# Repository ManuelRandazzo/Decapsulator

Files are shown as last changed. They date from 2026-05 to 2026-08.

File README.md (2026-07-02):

# Decapsulator
<p align="center">
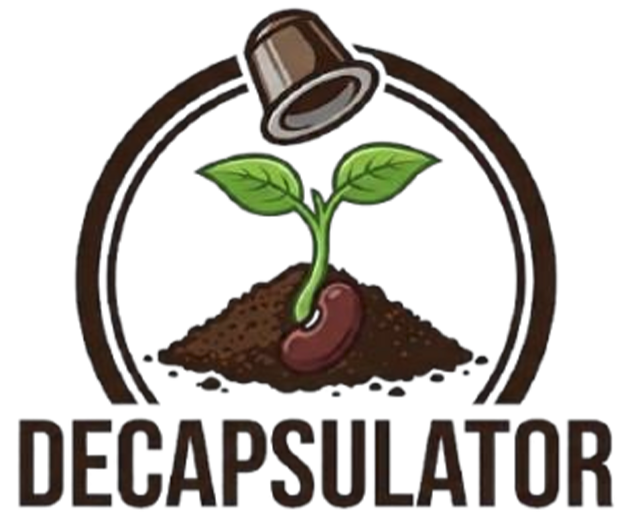
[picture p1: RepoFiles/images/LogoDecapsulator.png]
  
</p>

<p align="center">
  <em>Repo condiviso con il Gruppo 1 ITS 24-26 con programma del macchinario</em>
</p>

---

## Overview
**Decapsulator** è il prototipo di un macchinario nato con lo scopo principale di ridurre rifiuti secchi automatizzando un processo ripetitivo, che tende ad essere evitato e talvolta può diventare pericoloso se non si prestano le dovute attenzioni che è quello di aprire le capsule esauste per poter separare il caffè dall'involucro esterno.

**Sedi**: 
- **IIS Einaudi-Scarpa** : Via Sansovino, 6, 31044 Montebelluna (TV)
- **IPSIA Barsanti-Galilei** : Via Avenale, 6, 31033 Castelfranco Veneto (TV) 

---

## Intended Use 
Prototipo a scopo didattico, non destinato alla vendita o all'uso continuativo. In caso di vendita a scopo commerciale saranno da integrare tutti i dispositivi di sicurezza descritti nelle norme vigenti nella data di revisione e modifica del prototipo successiva a quella descritta dal documento di uso e manutenzione. 

---

## Features
- Automatizzazione della separazione delle capsule dal caffè
- Orientato alla facilità di utilizzo e di manutenzione
- FreeRTOS per avere un controllo real time del processo
- Sicurezza del macchinario
- Prototipo modulabile per diversi tipi di capsule cambiando pochissimi componenti
- Il suo sviluppo ha contribuito in piccola parte al mondo dell'Open Hardware di disegni CAD 3D.
- Design compatto rivolto ad un ambiente domestico

---

## Authors
- ***Manuel Randazzo*** - Firmware Designer, Backend Firmware Developer, Integration Developer, Firmware Tester, Electrical Designer, Electrical tester, Mechanical Designer, Documentation Contributor.
- ***Alessio Pisan*** - Electrical Designer, Electrical Tester, Frontend Firmware Developer, Backend Firmware Developer, Firmware Tester, Documentation Contributor.
- ***Riccardo Pavanetto*** - Mechanical Designer, Mechanical Designer
- ***Federico Dorigo*** - Scrum Master, Procurement Coordinator, Documentation Coordinator, Payroll Administrator
- ***Christian Poletti*** - Documentation Contributor
- ***Arun James Thanamcheril*** - Documentation Contributor

<p align="center">
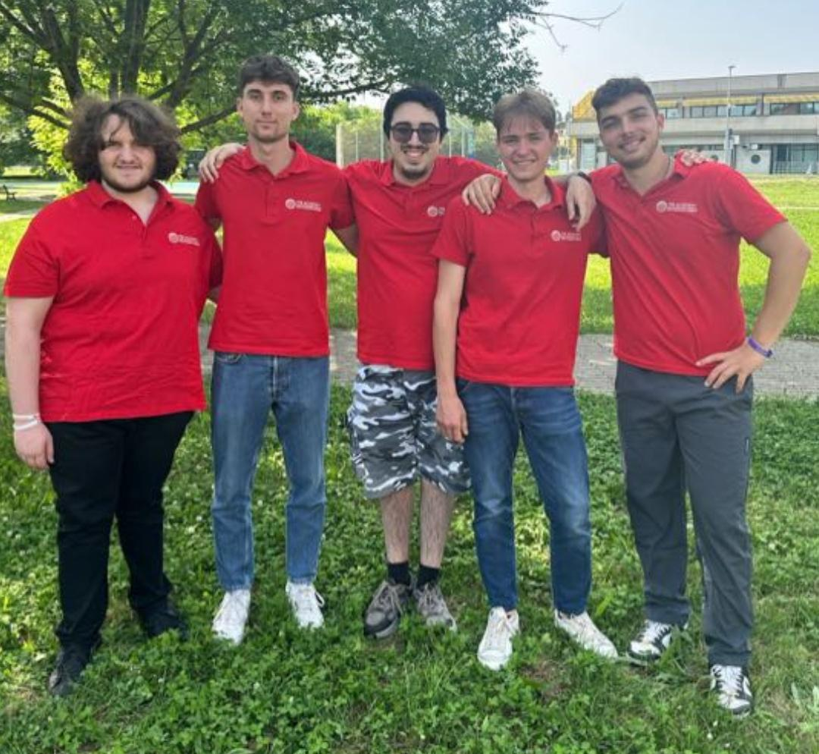
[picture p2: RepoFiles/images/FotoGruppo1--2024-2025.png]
  
</p>
<p align="center">
    <em>Foto del gruppo 1 ITS 24-25 - foto scattata nel 2025.</em>
    <em>Partendo da sinistra : Manuel, Christian, Alessio, Riccardo e Federico</em>
</p>

<p align="center">
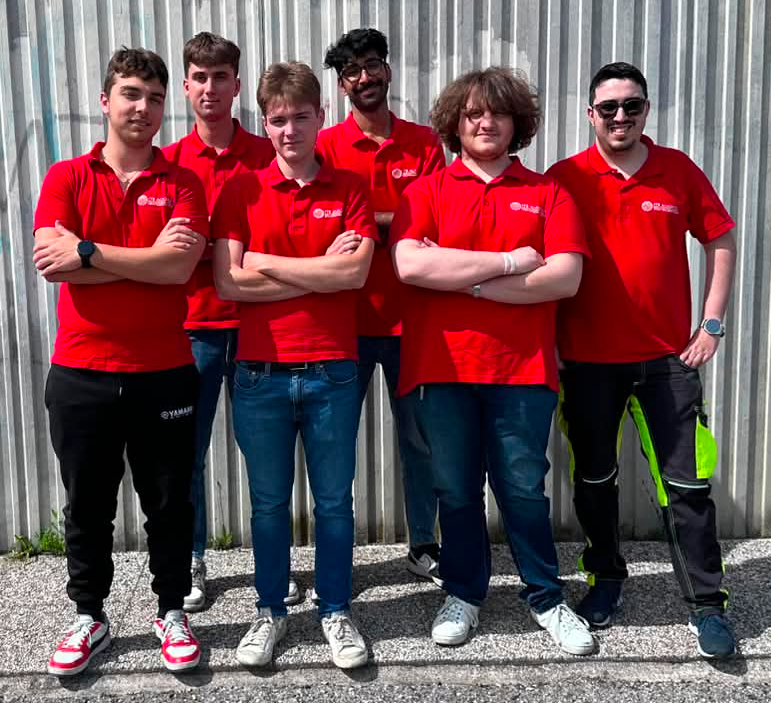
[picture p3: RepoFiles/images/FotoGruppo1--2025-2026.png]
  
</p>
<p align="center">
    <em>Foto del gruppo 1 ITS 25-26 - foto scattata nel 2026.</em>
    <em>Partendo da sinistra : Federico, Christian, Riccardo, Arun James, Manuel e Alessio</em>
</p>

---

## Dichiarazione Di Conformità CE Del Prototipo
Il presente prototipo è stato progettato seguendo i criteri di sicurezza delle varie direttive:  
- ***Direttiva Macchine 2006/42/CE***: Poiché l'apparecchio presenta organi in movimento, tra cui tamburo rotante, paratia di selezionatura servo-attivata e punzone, i quali comportano rischi meccanici.

- ***Direttiva Bassa Tensione (LVD) 2014/35/UE***: Consultata per la sicurezza dei componenti elettrici e dei circuiti di alimentazione.

- ***Direttiva Compatibilità Elettromagnetica (EMC) 2014/30/UE***: Applicabile per garantire che l’elettronica non interferisca con altre apparecchiature circostanti al macchinario.

- ***Direttiva RoHS 2011/65/UE***: Consultata per garantire l'assenza di sostanze pericolose nei componenti elettronici e nei materiali di apporto. 

Norme armonizzate applicate :
- ***UNI EN ISO 12100:2010***: Sicurezza del macchinario - Principi generali di progettazione - Valutazione e attenuazione del rischio. 

- ***UNI EN ISO 13857:2020***: Distanze di sicurezza per impedire il raggiungimento di zone pericolose con gli arti superiori (utilizzata per dimensionare l'imbocco delle capsule e i carter del tamburo).

- ***UNI EN ISO 14119:2013***: Dispositivi di interblocco associati ai ripari (utilizzata per la scelta e l'installazione del micro-switch di sicurezza sul coperchio).

- ***CEI EN 60204-1***: Sicurezza dell'equipaggiamento elettrico delle macchine (utilizzata per lo schema elettrico e funzionale). 

---

## Disegno Prototipo E Componenti Principali
- ### **Parte Meccanica**
<p align="center">
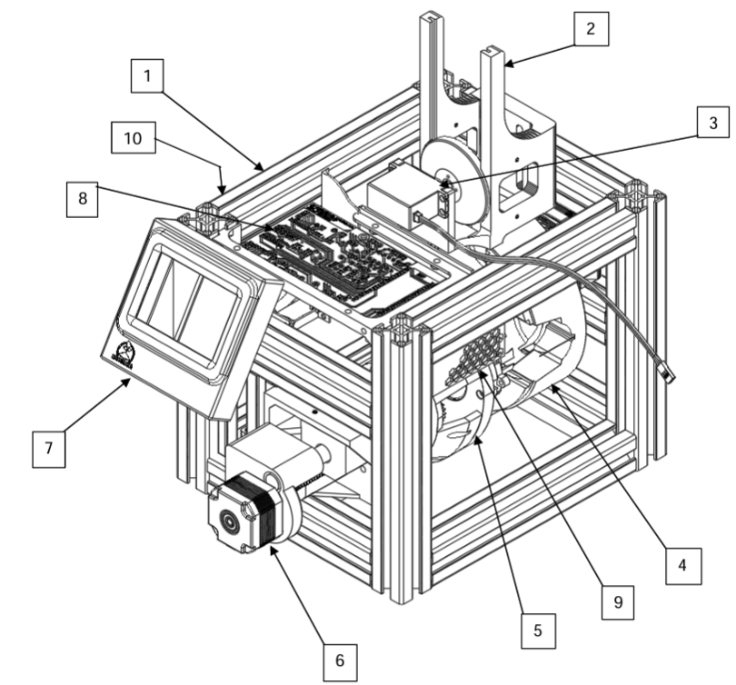
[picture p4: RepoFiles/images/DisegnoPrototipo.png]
  
</p>

<p align="center">
  <em>Figura 1 — Architettura generale del Decapsulator</em>
</p>
 
**Tabella Componenti :**

| N° |  Descrizione  |
|----|---|
| 1  | Profili in alluminio 30x30 cm |
| 2  | Magazzino verticale capsule |
| 3  | Paratia di selezionatura servoattivata del magazzino verticale |
| 4  | Tamburo di posizionamento |
| 5  | Zona di Punzonatura e Raschiatura |
| 6  | Motore passo-passo del Punzone e Raschiatore |
| 7  | Display dell’interfaccia uomo-macchina (HMI) |
| 8  | Scheda elettronica |
| 9  | Griglia di protezione parte elettronica |
| 10 | Ventola di raffreddamento (lato sinistro del macchinario) |

<p align="center">
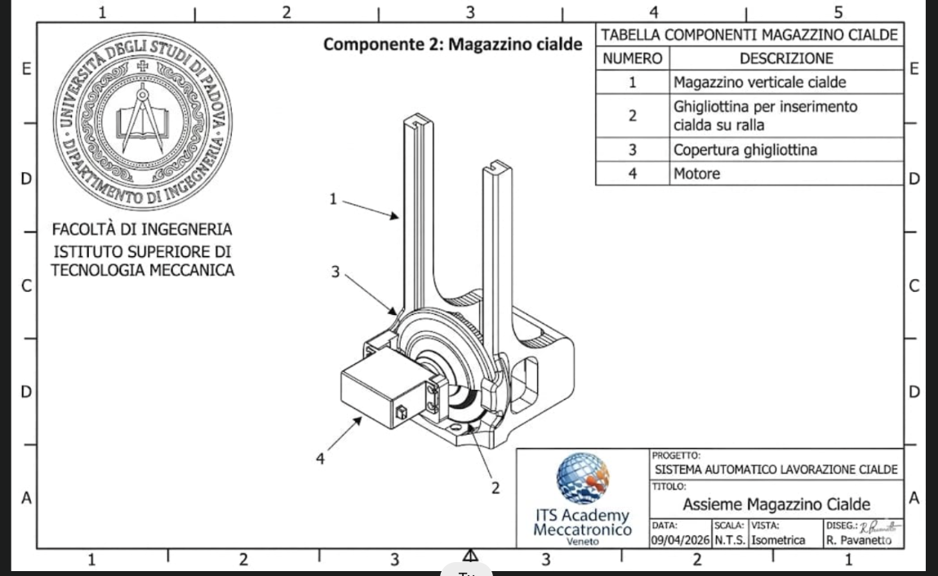
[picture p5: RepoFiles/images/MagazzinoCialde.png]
  
</p>

<p align="center">
  <em>Figura 2 — Magazzino Cialde : Serve per stoccare le capsule prima che vengano </em>
</p>

<p align="center">
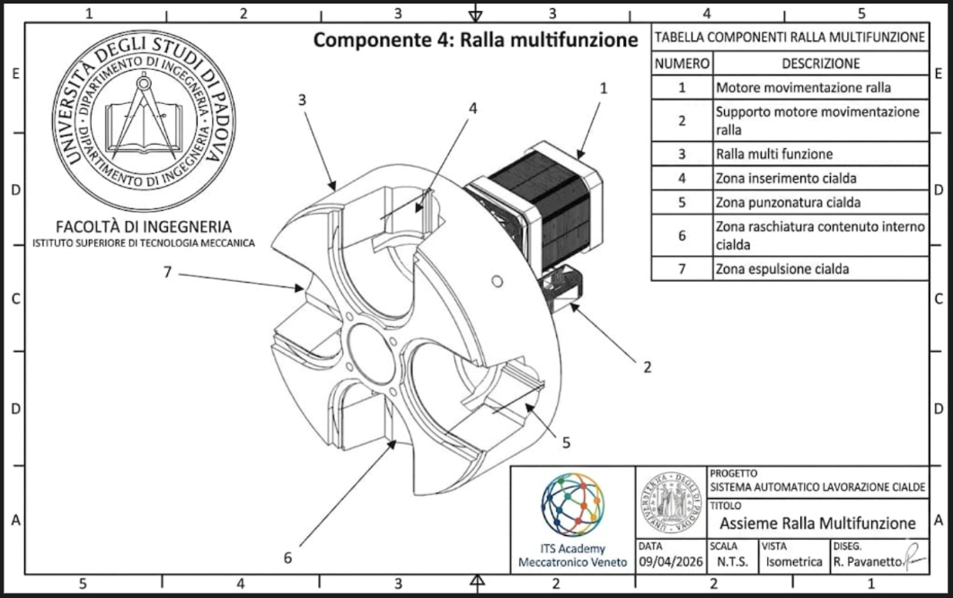
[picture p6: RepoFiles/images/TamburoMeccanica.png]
  
</p>

<p align="center">
  <em>Figura 3 — Tamburo : Serve per trasportare la capsula nelle varie fasi di lavorazione (Acquisizione, Punzonatura, Raschiatura, Espulsione)</em>
</p>

- ### **Parte Elettronica**

<p align="center">
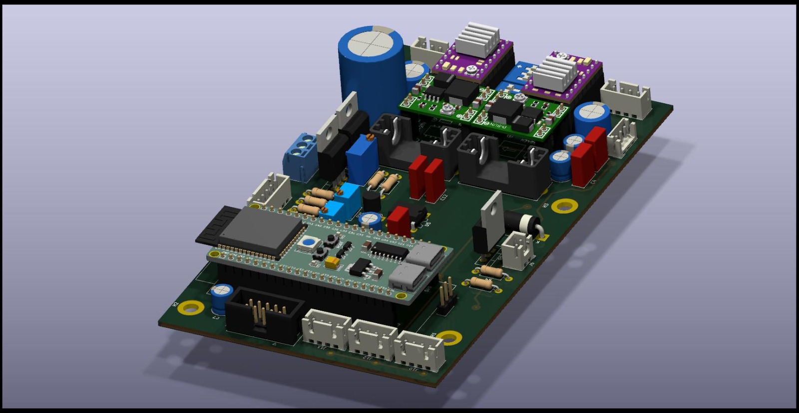
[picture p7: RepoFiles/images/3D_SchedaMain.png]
  
</p>

<p align="center">
  <em>Figura 4 — Scheda di controllo del Decapsulator</em>
</p>

<p align="center">
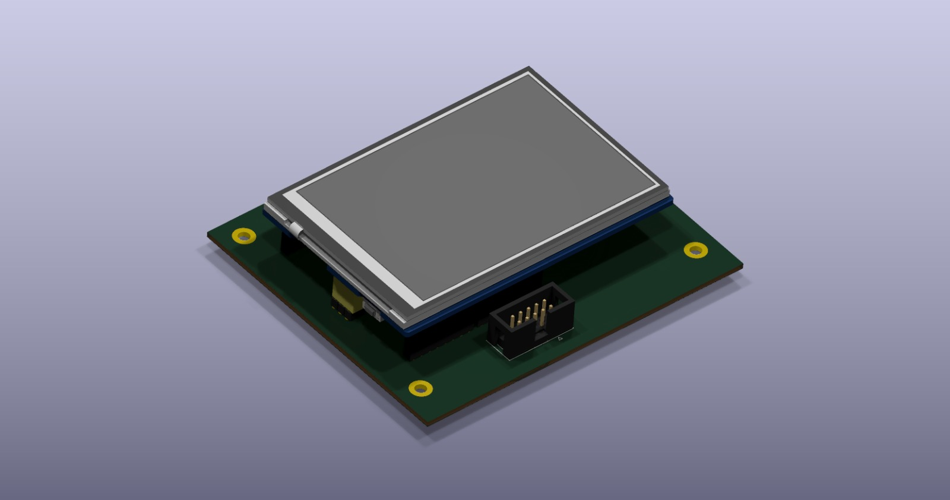
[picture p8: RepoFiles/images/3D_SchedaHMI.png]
  
</p>

<p align="center">
  <em>Figura 5 — Scheda HMI del Decapsulator</em>
</p>

<p align="center">
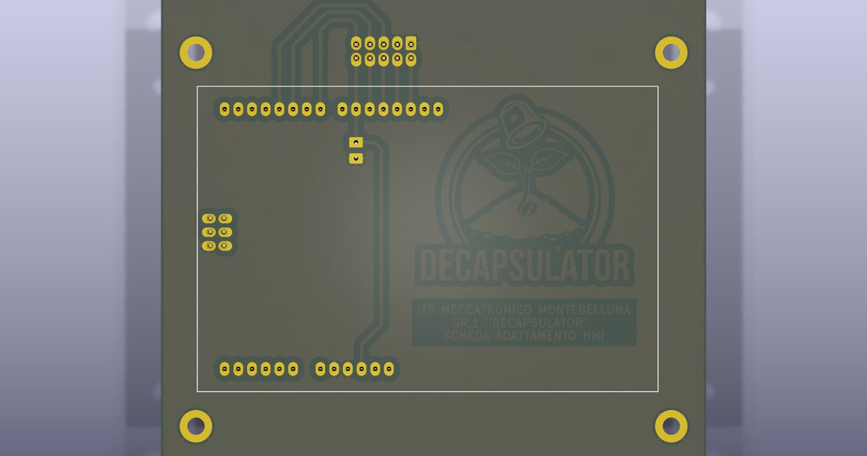
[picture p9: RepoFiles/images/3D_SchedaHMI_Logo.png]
  
</p>

<p align="center">
  <em>Figura 5 — Scheda HMI del Decapsulator - Vista retro</em>
</p>

<p align="center">
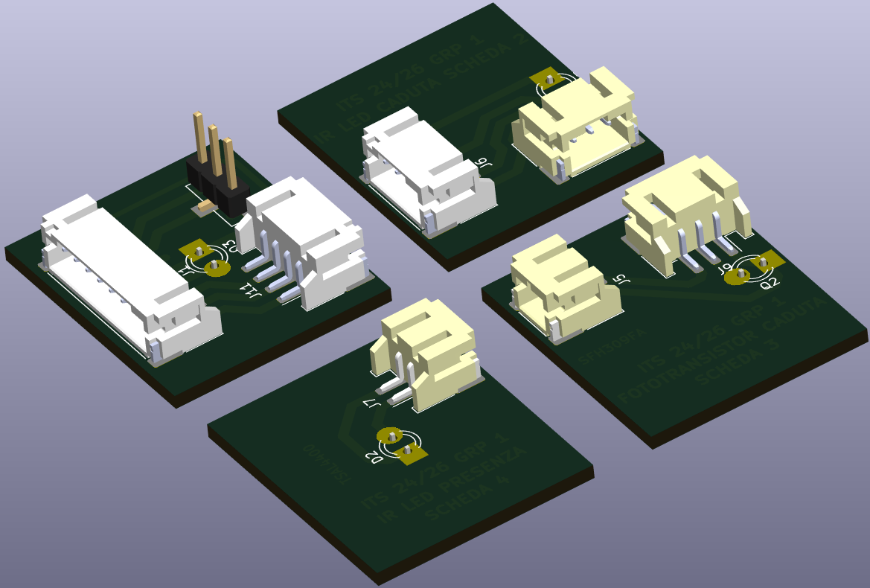
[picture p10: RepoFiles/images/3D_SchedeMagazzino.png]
  
</p>

<p align="center">
  <em>Figura 6 — Schede del "Magazzino Cialde" del Decapsulator, rappresentano due foto transistor e due LED IR, inoltre su una scheda è presente il connettore 3 poli del servomotore della "Paratia"</em>
</p>

---

## Sequenza Di Funzionamento Automatico Del Decapsulator
Il "Decapsulator" quando viene pilotato in modalità automatica per aprire le capsule di caffè segue questo diagramma :
<p align="center">
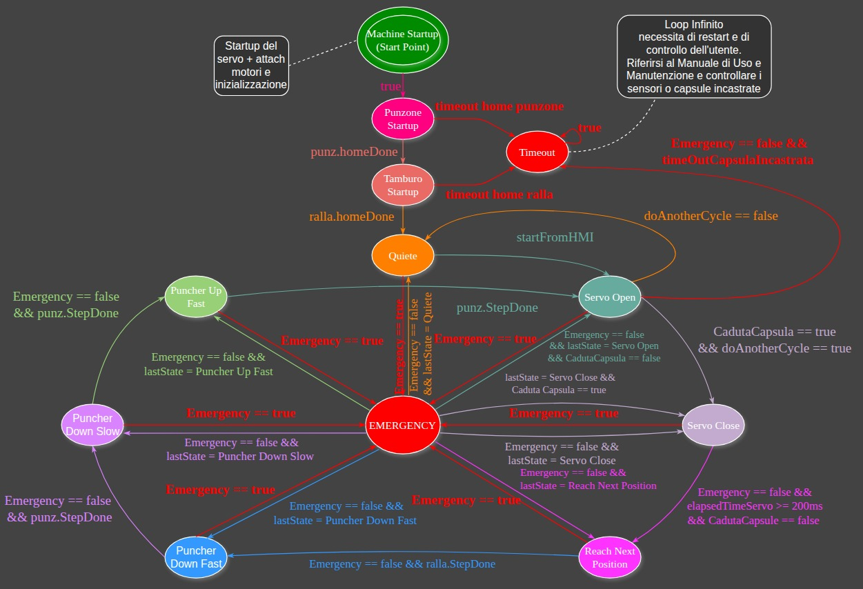
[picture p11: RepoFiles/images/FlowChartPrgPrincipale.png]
  
</p>

Il quale temporalmente si traduce in questa sequenza osservando i componenti :
<p align="center">
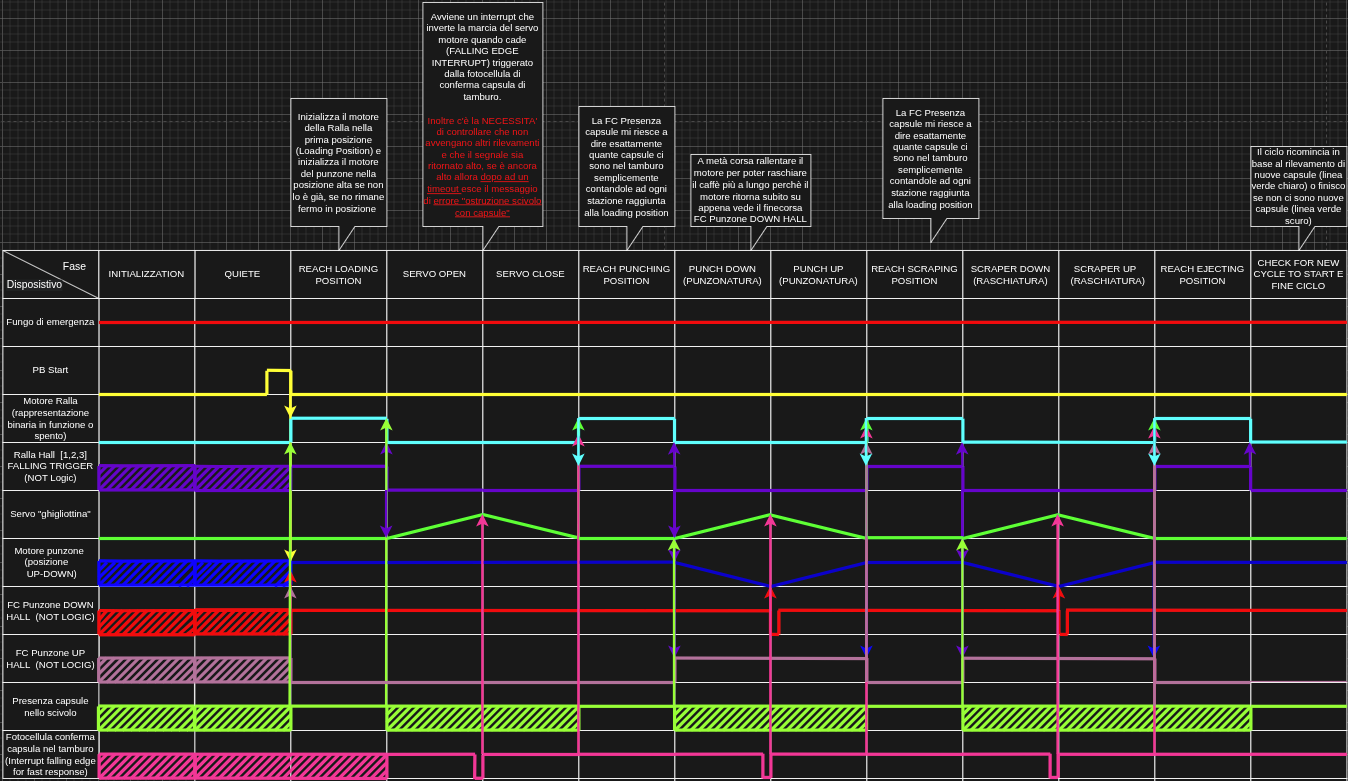
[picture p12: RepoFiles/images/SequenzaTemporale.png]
  
</p>

---

## Dati Sui Motori Utilizzati
Le librerie del driver DRV8825 sono state sviluppate interamente da Manuel Randazzo il quale si è preoccupato di studiare e testare l'hardware, consultare la documentazione ufficiale per poter integrare al meglio la libreria che può essere inclusa così :
```C++
#include "DRV8825_Decapsulator.hpp"
```
oppure includendo la libreria del Motion Controller che già utilizza internamente la precedente libreria e che permette una gestione più semplice del Motore :
```C++
#include "MotionControl.hpp"
```

**Flow chart MotionController**
<p align="center">
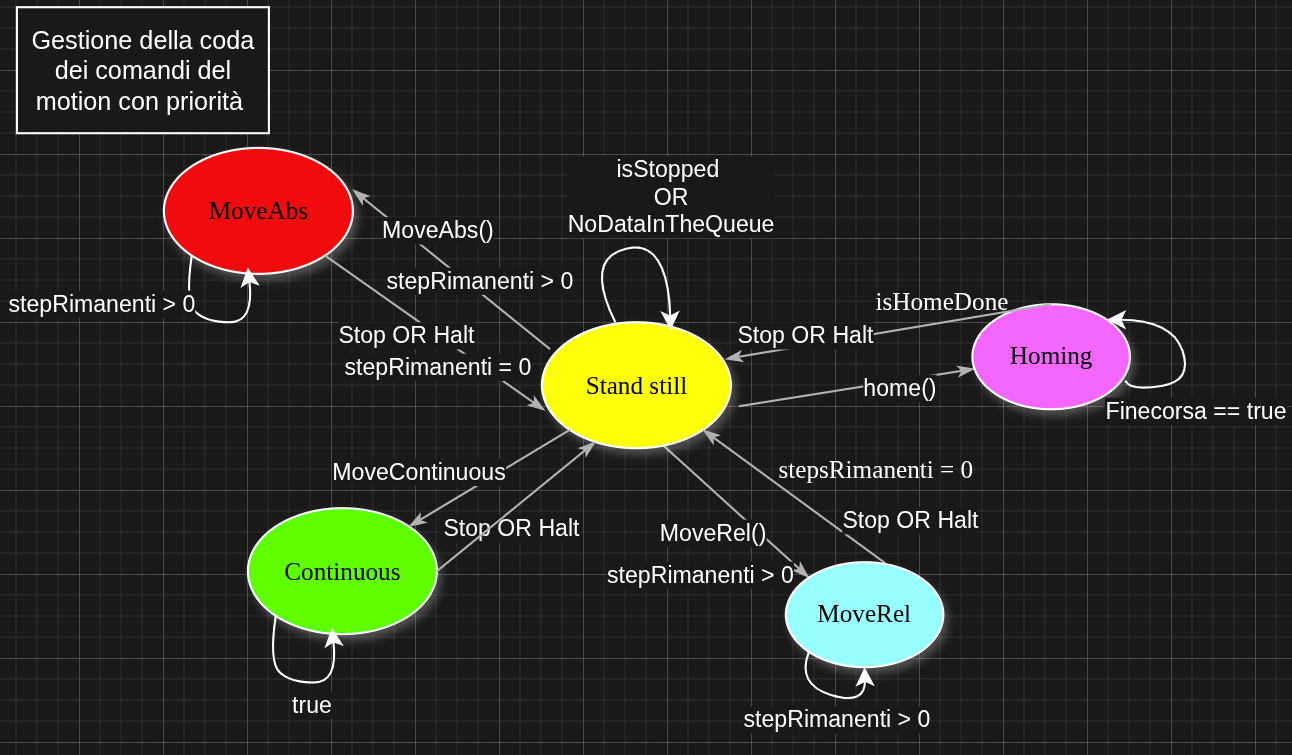
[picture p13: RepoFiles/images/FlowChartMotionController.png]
  
</p>

<p align="center">
  <em>Figura 7 — Flow chart MotionController</em>
</p>

**Simulazione Grafico Coppia-Velocità Motori Stepper**
<p align="center">
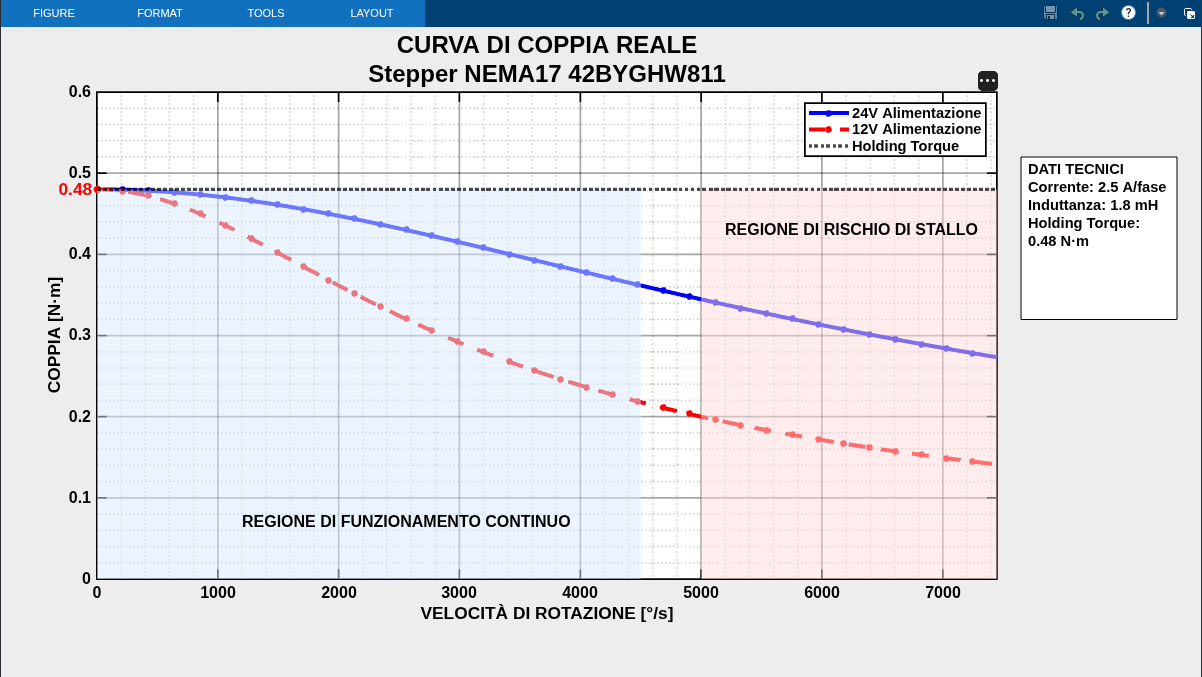
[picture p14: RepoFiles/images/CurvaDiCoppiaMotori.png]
  
</p>

<p align="center">
  <em>Figura 8 — Simulazione curva di coppia dei motori stepper con MATLAB</em>
</p>

---

## Diagnostica E Troubleshooting
Vi è una sezione dedicata per accedere alle impostazioni del manutentore direttamente dall'HMI del macchinario.

Per aiutare il manutentore ad individuare i problemi è possibile ottenere dei privilegi elevati attraverso un login e di conseguenza accedere alla pagina di diagnostica composta dal registro eventi (***Log***) del macchinario e dal movimento manuale (***Jog***) dei motori passo-passo del tamburo rotante e del punzone.

Per maggiori informazioni riguardo a come utilizzare la pagina di manutenzione consultare il manuale di uso e manutenzione alla sezione ***"9.4 Manutenzione tramite pagina di diagnostica sull’interfaccia utente"***.

- Come accedere alla pagina di diagnostica dalla GUI:  

1. Individuare nella pagina principale l’icona dell’ingranaggio indicata in figura
<p align="center">
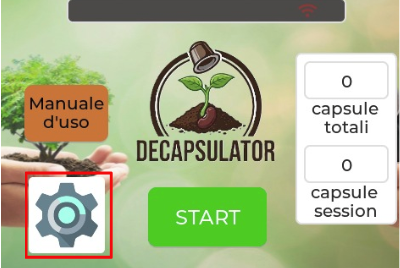
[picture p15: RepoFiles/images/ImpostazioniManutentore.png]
  
</p>

2. Inserire la password unica fornita ai manutentori specializzati
<p align="center">
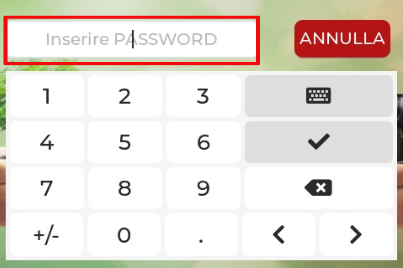
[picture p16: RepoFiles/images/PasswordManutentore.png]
  
</p>

- Come navigare nella pagina di diagnostica dalla GUI, riferimento alla sezione 9.4 del manuale di uso e manutenzione:  

1. Se si vogliono visualizzare i ***LOG*** del macchinario premere il pulsante "Logger" in alto a sinistra della pagina di diagnostica come in figura:
<p align="center">
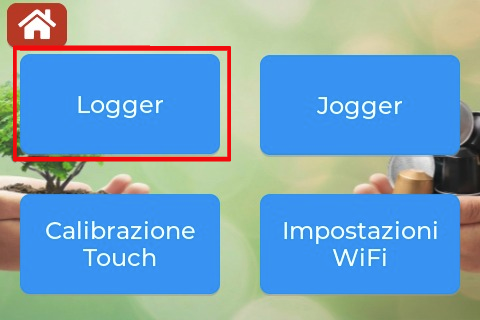
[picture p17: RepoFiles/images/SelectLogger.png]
  
</p>

1.1. Una volta selezionato il Logger si vedrà questa pagina da cui si potrà refreshare i logs oppure cancellarli per avere una pagina più pulita con i tasti in figura:
<p align="center">
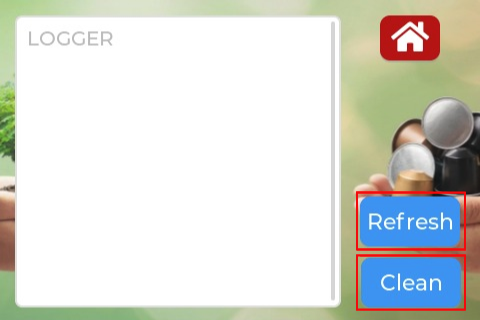
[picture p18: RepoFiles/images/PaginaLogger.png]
  
</p>

2. Se si vogliono comandare in modalità manuale i motori del macchinario con il ***JOG*** premere il pulsante "Jogger" in alto a destra della pagina di diagnostica come in figura:
<p align="center">
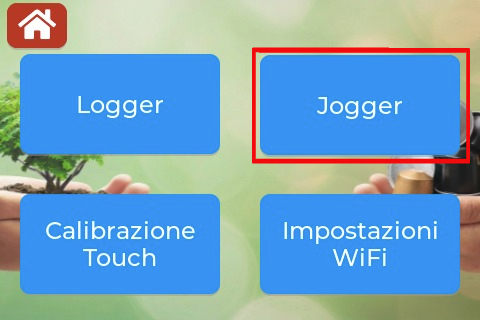
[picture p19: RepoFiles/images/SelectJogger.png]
  
</p>

2.1. Nota: non sarà possibile aggedere alla pagina "Jogger" se il ciclo automatico è stato avviato e non è stato messo in STOP oppure non è finito e si potrà vedere il seguente messaggio:
<p align="center">
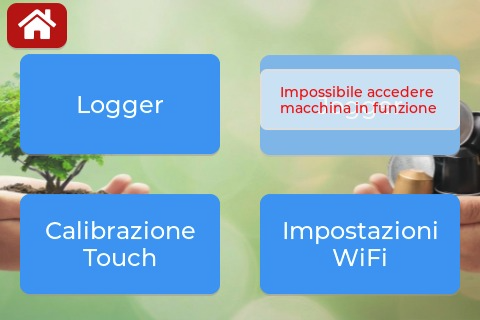
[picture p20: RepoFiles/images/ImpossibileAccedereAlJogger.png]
  
</p>

2.2. Una volta selezionato il Jogger si vedrà questa pagina da cui si potrà comandare indipendemente i motori e visualizzare gli stati dei sensori di finecorsa:
<p align="center">
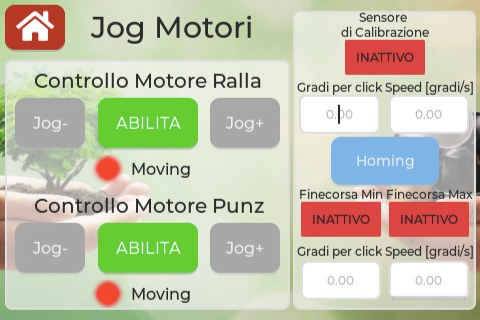
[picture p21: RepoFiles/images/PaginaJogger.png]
  
</p>

3. Se si vuole calibrare il display touch premere il pulsante in basso a sinistra della pagina di diagnostica e seguire le istruzioni fornite a display come in figura:
<p align="center">
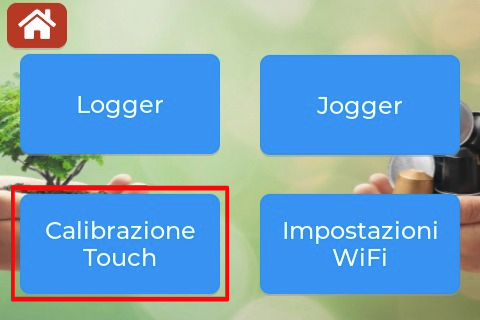
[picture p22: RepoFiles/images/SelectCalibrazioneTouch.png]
  
</p>

4. Se si vogliono inserire nuove credenziali per il WiFi premere il pulsante in basso a destra della pagina di diagnostica come in figura:
<p align="center">
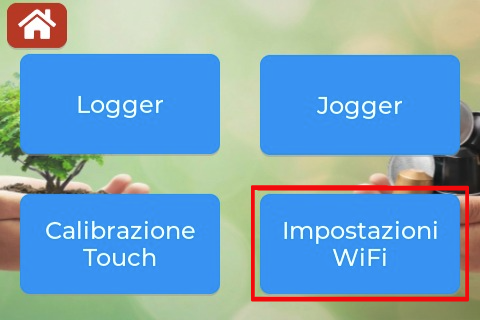
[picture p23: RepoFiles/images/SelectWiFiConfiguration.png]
  
</p>

4.1. Una volta selezionata la pagina di configurazione del WiFi verrà visualizzata questa pagina:
<p align="center">
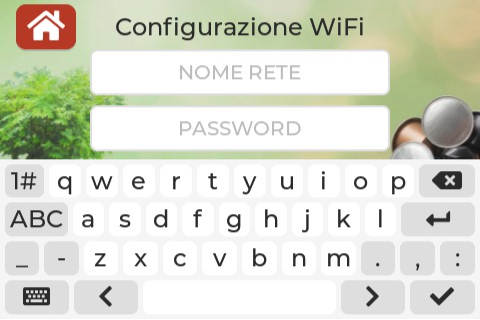
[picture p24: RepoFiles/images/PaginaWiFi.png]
  
</p>

<p align="center">
  <em>Nota : il WiFi consente al macchinario di fare l'upload del firmware tramite Over The Air (OTA), di far loggare in MQTT i messaggi del macchinario e soprattutto di sincronizzare il Real Time Clock (RTC) tramite server NTP così da visualizzare l'ora esatta</em>
</p>

---

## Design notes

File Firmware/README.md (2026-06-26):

# Decapsulator
<p align="center">
  
</p>

<p align="center">
  <em>Repo condiviso con il Gruppo 1 ITS 24-26 con programma del macchinario</em>
</p>

---

## Overview
**Decapsulator** è il prototipo di un macchinario nato con lo scopo principale di ridurre rifiuti secchi automatizzando un processo ripetitivo, che tende ad essere evitato e talvolta può diventare pericoloso se non si prestano le dovute attenzioni che è quello di aprire le capsule esauste per poter separare il caffè dall'involucro esterno.

**Sedi**: 
- Via Sansovino, 6, 31044 Montebelluna (TV)
- Via Avenale, 6, 31033 Castelfranco Veneto (TV) 

---

## Intended use 
Prototipo a scopo didattico, non destinato alla vendita o all'uso continuativo. In caso di vendita a scopo commerciale saranno da integrare tutti i dispositivi di sicurezza descritti nelle norme vigenti nella data di revisione e modifica del prototipo successiva a quella descritta dal documento di uso e manutenzione. 

---

## Features
- Automatizzazione della separazione delle capsule dal caffè
- Orientato alla facilità di utilizzo e di manutenzione
- FreeRTOS per avere un controllo real time del processo
- Sicurezza del macchinario
- Prototipo modulabile per diversi tipi di capsule cambiando pochissimi componenti
- Il suo sviluppo ha contribuito in piccola parte al mondo dell'Open Hardware di disegni CAD 3D.
- Design compatto rivolto ad un ambiente domestico

---

## Authors
- ***Manuel Randazzo*** - Software Designer, Backend Software Developer, Integration Developer, Software Tester, Electrical Designer, Electrical tester, Mechanical Designer.
- ***Alessio Pisan*** - Electrical Designer, Electrical Tester, Frontend Software Developer, Backend Software Developer, Software Tester.
- ***Riccardo Pavanetto*** - Mechanical Designer, Mechanical Designer
- ***Federico Dorigo*** - Scrum Master, Procurement Coordinator, Documentation Coordinator, Payroll Administrator
- ***Christian Poletti*** - Documentation Contributor
- ***Arun James Thanamcheril*** - Documentation Contributor

<p align="center">
  
</p>
<p align="center">
    <em>Foto del gruppo 1 ITS 24-25 - foto scattata nel 2025</em>
    <em>Partendo da sinistra : Manuel, Christian, Alessio, Riccardo e Federico</em>
</p>

<p align="center">
  
</p>
<p align="center">
    <em>Foto del gruppo 1 ITS 25-26 - foto scattata nel 2026</em>
    <em>Partendo da sinistra : Federico, Christian, Riccardo, Arun James, Manuel e Alessio</em>
</p>

---

## Dichiarazione di Conformità CE del prototipo
Il presente prototipo è stato progettato seguendo i criteri di sicurezza delle varie direttive:  
- ***Direttiva Macchine 2006/42/CE***: Poiché l'apparecchio presenta organi in movimento, tra cui tamburo rotante, paratia di selezionatura servo-attivata e punzone, i quali comportano rischi meccanici.

- ***Direttiva Bassa Tensione (LVD) 2014/35/UE***: Consultata per la sicurezza dei componenti elettrici e dei circuiti di alimentazione.

- ***Direttiva Compatibilità Elettromagnetica (EMC) 2014/30/UE***: Applicabile per garantire che l’elettronica non interferisca con altre apparecchiature circostanti al macchinario.

- ***Direttiva RoHS 2011/65/UE***: Consultata per garantire l'assenza di sostanze pericolose nei componenti elettronici e nei materiali di apporto. 

Norme armonizzate applicate :
- ***UNI EN ISO 12100:2010***: Sicurezza del macchinario - Principi generali di progettazione - Valutazione e attenuazione del rischio. 

- ***UNI EN ISO 13857:2020***: Distanze di sicurezza per impedire il raggiungimento di zone pericolose con gli arti superiori (utilizzata per dimensionare l'imbocco delle capsule e i carter del tamburo).

- ***UNI EN ISO 14119:2013***: Dispositivi di interblocco associati ai ripari (utilizzata per la scelta e l'installazione del micro-switch di sicurezza sul coperchio).

- ***CEI EN 60204-1***: Sicurezza dell'equipaggiamento elettrico delle macchine (utilizzata per lo schema elettrico e funzionale). 

---

## Disegno prototipo e Componenti Principali
- ### **Parte Meccanica**
<p align="center">
  
</p>

<p align="center">
  <em>Figura 1 — Architettura generale del Decapsulator</em>
</p>
 
**Tabella Componenti :**

| N° |  Descrizione  |
|----|---|
| 1  | Profili in alluminio 30x30 cm |
| 2  | Magazzino verticale capsule |
| 3  | Paratia di selezionatura servoattivata del magazzino verticale |
| 4  | Tamburo di posizionamento |
| 5  | Zona di Punzonatura e Raschiatura |
| 6  | Motore passo-passo del Punzone e Raschiatore |
| 7  | Display dell’interfaccia uomo-macchina (HMI) |
| 8  | Scheda elettronica |
| 9  | Griglia di protezione parte elettronica |
| 10 | Ventola di raffreddamento (lato sinistro del macchinario) |

<p align="center">
  
</p>

<p align="center">
  <em>Figura 2 — Magazzino Cialde : Serve per stoccare le capsule prima che vengano </em>
</p>

<p align="center">
  
</p>

<p align="center">
  <em>Figura 3 — Tamburo : Serve per trasportare la capsula nelle varie fasi di lavorazione (Acquisizione, Punzonatura, Raschiatura, Espulsione)</em>
</p>

- ### **Parte Elettronica**

<p align="center">
  
</p>

<p align="center">
  <em>Figura 4 — Scheda di controllo del Decapsulator</em>
</p>

<p align="center">
  
</p>

<p align="center">
  <em>Figura 5 — Scheda HMI del Decapsulator</em>
</p>

<p align="center">
  
</p>

<p align="center">
  <em>Figura 5 — Scheda HMI del Decapsulator - Vista retro</em>
</p>

<p align="center">
  
</p>

<p align="center">
  <em>Figura 6 — Schede del "Magazzino Cialde" del Decapsulator, rappresentano due foto transistor e due LED IR, inoltre su una scheda è presente il connettore 3 poli del servomotore della "Paratia"</em>
</p>

---

## Dati Sui Motori Utilizzati
Le librerie del driver DRV8825 sono state sviluppate interamente da Manuel Randazzo il quale si è preoccupato di studiare e testare l'hardware, consultare la documentazione ufficiale per poter integrare al meglio la libreria che può essere inclusa così :
```C++
#include "DRV8825_Decapsulator.hpp"
```
oppure includendo la libreria del Motion Controller che già utilizza internamente la precedente libreria e che permette una gestione più semplice del Motore :
```C++
#include "MotionControl.hpp"
```

**Flow chart MotionController**
<p align="center">
  
</p>

<p align="center">
  <em>Figura 7 — Flow chart MotionController</em>
</p>

**Simulazione Grafico Coppia-Velocità Motori Stepper**
<p align="center">
  
</p>

<p align="center">
  <em>Figura 8 — Simulazione curva di coppia dei motori stepper con MATLAB</em>
</p>

---

## Diagnostica e Troubleshooting
Vi è una sezione dedicata per accedere alle impostazioni del manutentore direttamente dall'HMI del macchinario.

Per aiutare il manutentore ad individuare i problemi è possibile ottenere dei privilegi elevati attraverso un login e di conseguenza accedere alla pagina di diagnostica composta dal registro eventi (***Log***) del macchinario e dal movimento manuale (***Jog***) dei motori passo-passo del tamburo rotante e del punzone. 

Come accedervi:  
1. Individuare nella pagina principale l’icona dell’ingranaggio indicata in figura
<p align="center">
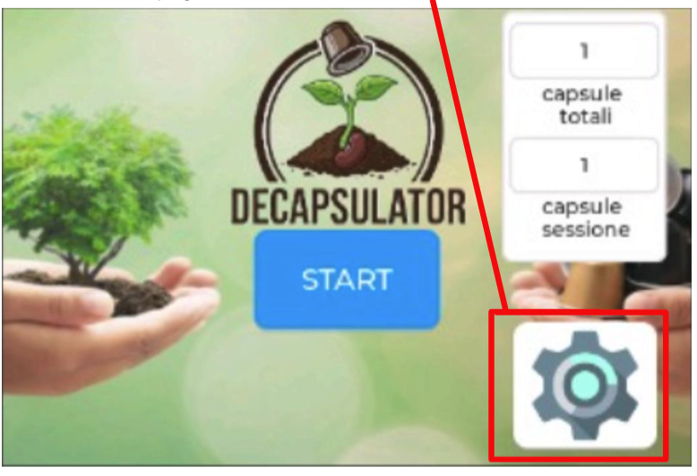
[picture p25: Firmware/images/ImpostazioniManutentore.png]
  
</p>
2. Inserire la password unica fornita ai manutentori specializzati
<p align="center">
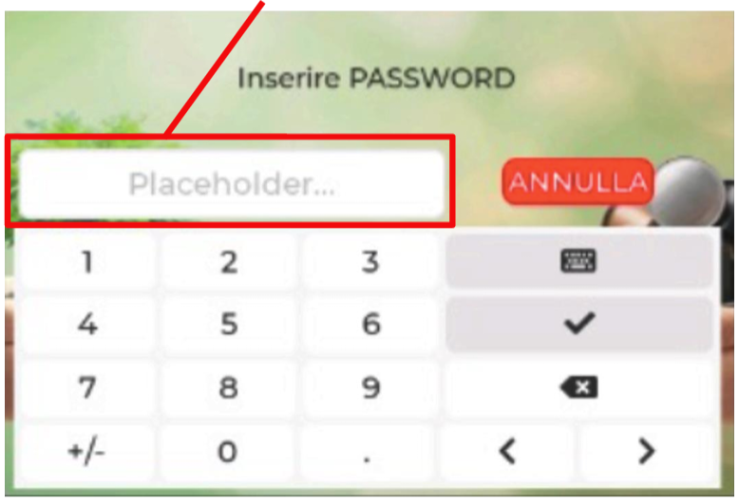
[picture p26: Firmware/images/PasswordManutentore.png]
  
</p>

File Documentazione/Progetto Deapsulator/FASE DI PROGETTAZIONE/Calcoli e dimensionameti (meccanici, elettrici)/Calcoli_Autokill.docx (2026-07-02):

Dimensionamento circuito di Autokill nel Decapsulator

Componenti :

- MOSFET CANALE P (IRF9540N)
- Amplificatore Operazionale (LM311)
- Transistor a giunzione bipolare (BC547)
- Potenziometro multigiro
- Resistenze Varie

Calcolo potenza dissipata e incremento di temperatura del MOSFET canale P IRF9540N

CONSIDERAZIONI INIZIALI

Vi è da considerare che la corrente non scorre sempre ma solo una volta per pochi millisecondi quando si spegne il macchinario oppure quando salta la corrente, quindi il MOSFET sarà nel tempo prevalentemente spento e di conseguenza sarà sempre freddo

legenda simboli per il calcolo del MOSFET

- Resistenza tra Drain e Source quando il mosfet è acceso = RDSon [Ω]

- Corrente tra Drain e Source quando il mosfet è acceso = IDS [A]

- Potenza dissipata = PD [W]

- Resistenza termica da giunzione ad ambiente RθJA [°C/W]

- Incremento di temperatura per ogni Watt dissipato = TW [°C]

Calcoli:

RDSon e RθJA sono date dal datasheet ed equivalgono a :

- RDSon=0,117 Ω
- RθJA = 62 °C/W

IDS è stata ipotizzata (sovradimensionata) a :

- IDS = 0,5A

La potenza dissipata è stata calcolata con la seguente formula :

- PD = IDS * RDSon = 0,5 * 0,117 = 29,25 W

L’Incremento di temperatura per ogni Watt dissipato è stata calcolato con la seguente formula :

- TW = PD / 1000 * RθJA = 29,25 / 1000 * 62 = 1,8135 °C

Calcolo del Transistor BJT BC547 che pilota il MOSFET canale P IRF9540N

CONSIDERAZIONI INIZIALI

La tensione applicata al source (VBAT) del mosfet è di 9V e per garantire che il mosfet si accenda/spenga la resistenza di pullup del gate è stata colleganda con un reoforo alla VBAT e con l’altro al collettore del BC547 e quest’ultimo è stato configurato come una NOT logica, per cui se il segnale sul BC547 è alto allora sul MOSFET il segnale sarà basso ed essendo un MOSFET canale P questo farà quindi scorrere corrente tra drain e source. La base del BJT è comandata da un GPIO di un ESP32-S3 la quale fornisce circa 3,3V e 40mA MASSIMI ed essendo quindi un interruttore verrà presa in considerazione una VCE pari alla VCE(SAT) fornita dal datasheet.

legenda simboli per il calcolo del Transistor BJT Pilota

- Tensione sul collettore = VBAT [V]
- Tensione sulla base = VGPIO [V]
- Tensione collettore-emettitore = VCE(SAT) [V]
- Tensione base-emettitore = VBE [V]
- Guadagno di corrente statico = hFE
- Corrente sul collettore = IC [A]
- Corrente sulla base = IB [A]
- Resistenza sul collettore = RC [Ω]
- Resistenza sulla base = RB [Ω]

Calcoli:

Informazioni date dal datasheet e/o ipotizzate :

- VBAT = 9V
- VGPIO = 3,3V
- VCE(SAT) = 0,2V
- VBE = 0,6V
- hFE = 10
- IC = 600µA

La resistenza da mettere sul collettore si calcola con :

- RC = (VBAT – VCE(SAT)) / IC = (9 – 0,2) / 600*10^-6 = 8,8 / 600*10^-6 = 14,666kΩ
- scelgo RC=15kΩ
- IC(REALE) = (VBAT – VCE(SAT)) / RC = (9 – 0,2) / 15*10^3 = 8,8 / 15*10^3 = 586µA

La corrente che deve scorrere sulla base si calcola con :

- IB > IC(REALE) / hFE → IB > 586*10^-6 / 10 → IB > 58,6µA
- RB(MAX) = (VGPIO – VBE) / IB(MIN) = (3,3 – 0,6) / 58,6*10^-6 = 2,7 / 58,6*10^-6 = 46kΩ per cui scelgo RB = 33kΩ per saturare meglio e rimanendo sotto la soglia dei 40mA del GPIO
- IB(REALE) = (VGPIO – VBE) / RB = (3,3 – 0,6) / 33*10^3 = 2,7 / 33*10^3 = 82µA

Ricalcolo il guadagno di corrente statico reale con le correnti trovate :

- hFE(REALE) = IC(REALE) / IB(REALE) = 586*10^-6 / 82*10^-6 = 7,15

Calcolo dell’Amplificatore Operazionale LM311 in configurazione Comparatore

CONSIDERAZIONI INIZIALI

l’OPAMP è in configurazione comparatore, infatti questo compara la soglia in ingresso dell’alimentazione VALIM (24V DC) e la VREF determinata dall’ESP32 di 3,3V.

L’alimentazione dell’OPAMP è stata scelta pari a 5V (Vcc) perché i segnali da comparare vengono rilevati solo se Vsegnali < Valim – 1,5V per cui la tensione massima rilevata dagli ingressi dell’opamp è Vsegnali = 5 – 1,5 = 3,5V per cui vi è un potenziometro da 200kΩ (scelto perché così consuma poca corrente) che regola l’ingresso non invertente al comparatore (In+); il tutto è coerente con l’ipotesi. Il comparatore deve essere dotato di una resistenza di pull-up da 100kΩ (RPU), scelta perché così consuma poca corrente, tra i 3,3V (VGPIO) e il collettore dell’LM311 rendendolo così praticamente una porta NOT, per cui si vuole che quando V+ < VREF il pin dell’ESP32 riceva un falling e per ciò la scelta di avere V+ sull’ingresso non invertente (In+) dell’OPAMP e la VREF sul pin invertente (In-).

legenda simboli per il calcolo del Partitore di tensione del In+ del comparatore

- Tensione in ingresso al partitore = VALIM [V]
- Tensione alla quale si spegne il circuito = VTH_PWROFF [V]
- Tensione di uscita collettore LM311 = Vout
- Tensione di soglia ESP32 GPIO livello basso = VTH_LOW [V]
- Corrente assorbita dal partitore = Iassorbita [A]
- Tensione in uscita dal partitore (potenziometro) = V+ [V]
- Resistenza 1 (prima metà del potenziometro) = RPOT1 [Ω]
- Resistenza 2 (seconda metà del potenziometro) = RPOT2[Ω]

Calcoli:

Informazioni date dal datasheet e/o ipotizzate :

- VALIM = 24V
- VGPIO = 3,3V
- VTH_PWROFF = 18V
- ITOTassorbita < 400µA
- VTH_LOW = 0,825V
- Quando V+ < VREF allora Vout ≤ VTH_LOW
- VCE(SAT) = 0,2V

Calcolo corrente assorbita dal partitore in condizioni normali (non di spegnimento) :

- IPOTassorbita(REALE) = VALIM / (RPOT1+ RPOT2) = VALIM / RPOT = 24 / 200*10^3 = 120µA

Calcolo delle resistenze del potenziometro :

- V+ < VREF → scelgo V+ = 3,2V → V+ < VTH_PWROFF * RPOT2 / (RPOT1+ RPOT2) →

V+ < VTH_PWROFF * RPOT2 / RPOT → 3,2 < 18 * RPOT2 / 200*10^3 →

3,2 * 200*10^3 / 18 < RPOT2 → RPOT2 > 35,555kΩ scelgo RPOT2 = 36kΩ

- RPOT1 = RPOT – RPOT2 = 200*10^3 – 36*10^3 = 164kΩ

Corrente assorbita dalla resistenza di pull-up sul collettore dell’LM311 :

- IPUassorbita(MAX) = ITOTassorbita – IPOTassorbita = 400*10^(-6) – 120*10^(-6) = 280µA
- IPUassorbita(MAX) < (VGPIO – VCE(SAT) ) / RPU → RPU > (VGPIO – VCE(SAT) ) / IPUassorbita(MAX) →

RPU > (3,3 – 0,2) / 280*10^(-6) = 3,1 / 280*10^(-6) = 11kΩ

- Scelgo RPU = 100kΩ per cui IPUassorbita(REALE) = (VGPIO – VCE(SAT) ) / RPU = (3,3 – 0,2) / 100*10^3 = 31µA

Corrente assorbita totale dal circuito di comparazione

- ITOTassorbita(REALE) = IPOTassorbita(REALE) + IPUassorbita(REALE) = 120*10^(-6) + 31*10^(-6) = 151µA

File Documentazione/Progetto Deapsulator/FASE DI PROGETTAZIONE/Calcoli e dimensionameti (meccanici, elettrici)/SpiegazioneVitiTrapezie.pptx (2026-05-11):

## Robe da Meccanici… Viti Trapezie

(Sono solo un elettronico mancato)

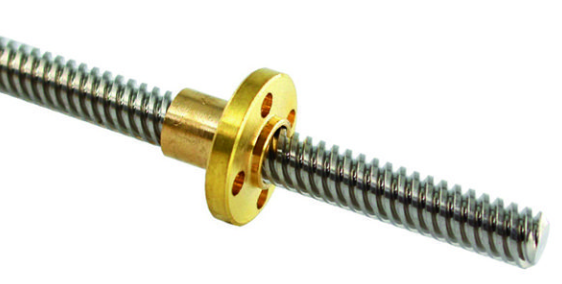
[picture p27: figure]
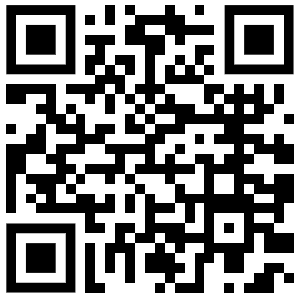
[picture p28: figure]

Chiocciola o madrevite

Vite Trapezoidale

## Problema posto :

- Trovare la massima forza che può sviluppare il punzone conoscendo la coppia massima del motore
- Capire se sia sicuro togliere la coppia al motore in caso di emergenza (come da normativa macchine) senza caduta accidentale del carico

## Dati sul motore del punzone :

Coppia a basse velocità ( < 200 rpm) ~= 70% * holding Torque ~= 70% * 4800 = 3360 g/cm
(sarebbe meglio guardare il grafico della curva di coppia per sapere a quanto corrisponde la coppia dinamica agli rpm a cui deve girare il motore)
Coppia Motore Statica = Ms [Nm] = = 0,471 Nm
Coppia Motore Dinamica = M [Nm] = ~= 0,33 Nm

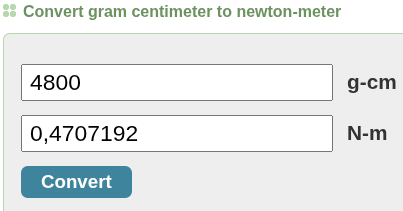
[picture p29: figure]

chiamata M perché è un “MOMENTO” essendo che
Momento = Coppia = (Forza * braccio) = Nm

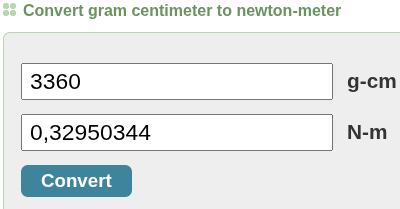
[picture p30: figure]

## Dati Sulla vite Trapezoidale :

- p=passo=2mm
- Dm=diametro medio= 7mm
- = 2 / (7*3,14) ~= 0,09
- tg ɑ= Tangente dell’angolo riferito all’inclinazione elica della filettatura

Geometria Vite

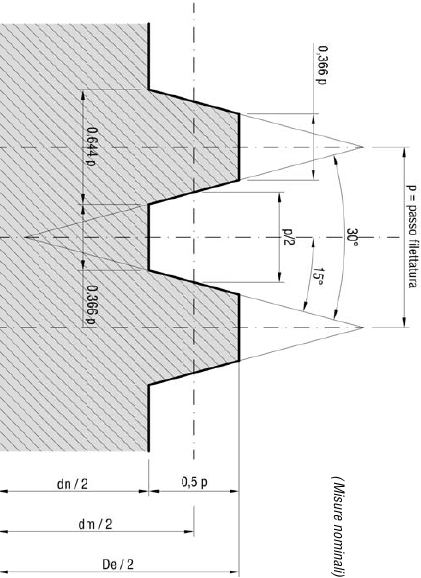
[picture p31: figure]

## Zoom sull’angolo dell’elica

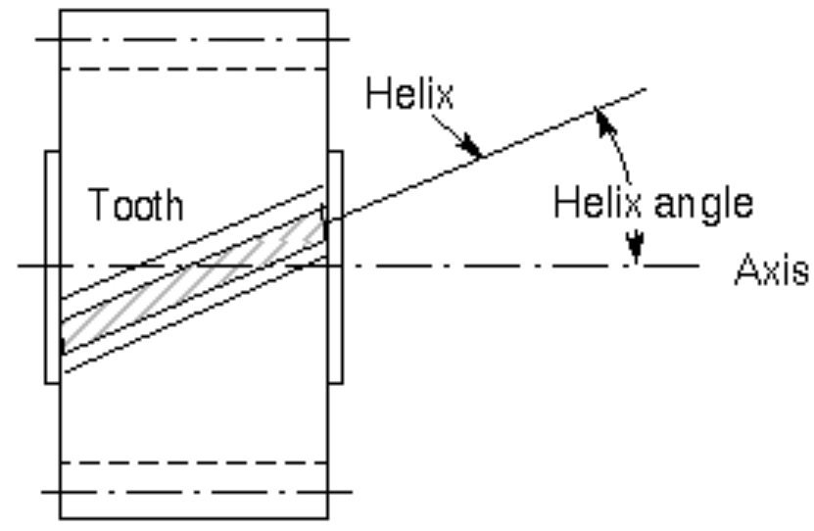
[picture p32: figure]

## Dati Utili Sulla Chiocciola :

- f=coeff. D’attrito tra chiocciola e madrevite (ad esempio noi abbiamo vite in acciaio e madrevite (detta anche chiocciola) in ottone e il tutto senza lubrificazione per cui dalla tabella scegliamo Steel,dry (vite in acciaio non lubrificata) colonna Brass (madrevite ottone)

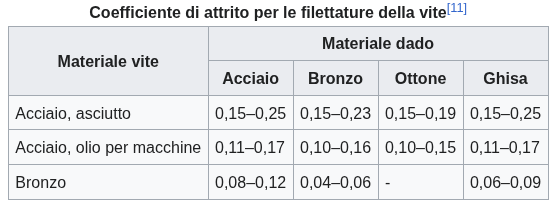
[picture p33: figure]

Scegliamo il caso peggiore e lo arrotondiamo a
f=0.2

## Cosa chiede il Manuale Tecnico :

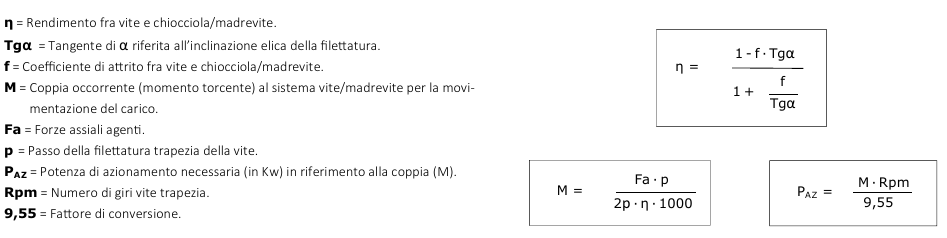
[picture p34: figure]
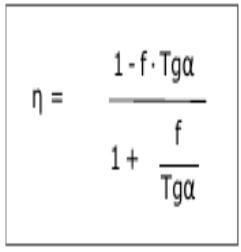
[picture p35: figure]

QR Code Manuale Tecnico
(pagina 17)

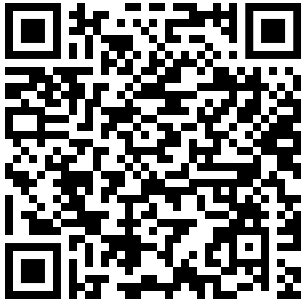
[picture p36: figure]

## Rendimento vite-madrevite:

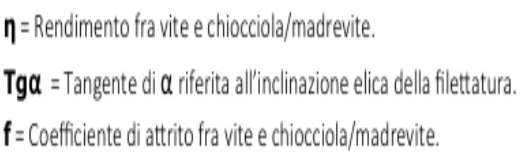
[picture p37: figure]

ɳ = = 0,982 / 3,22 = 0,305

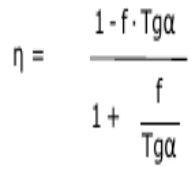
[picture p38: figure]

Posso già controllare se sia sicuro togliere la coppia al motore calcolando il rendimento non preferenziale (ɳnon_preferenziale = quando è il carico a tirare giù
el faxiòl (termine tecnico per dire il fagiolo) )

ɳnon_preferenziale = 2 - ( 1/ɳ ) = 2 - ( 1/0,305) = 2 – 3,28 = -1,28
(essendo non solo basso ma addirittura negativo so che non torna indietro e quindi posso togliere la coppia come da normativa macchine)

## Trovare la forza partendo dalla coppia :

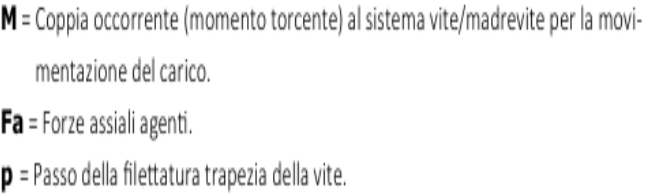
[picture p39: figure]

2p = 2*π [sì, è facile confondersi
(sono dei criminali.) ]

Formula Inversa per trovare la Forza (Fa)

[in mm]

Fa= = =
Fa = 316 N
(partendo da 0,33N del motore non è male)

Tradotto in chilogrammi : Fa[kg] = Fa[N] / g[m/s²] = 316 / 9,80665 = 32,22kg
Di forza applicati ad un carico dinamico (in statico con M=0,471Nm fa 46kg)

g=Accelerazione di gravità

## RESISTENZA A COMPRESSIONE DELLA VITE TRAPEZIA IN RELAZIONE AL TIPO DI VINCOLO UTILIZZATO

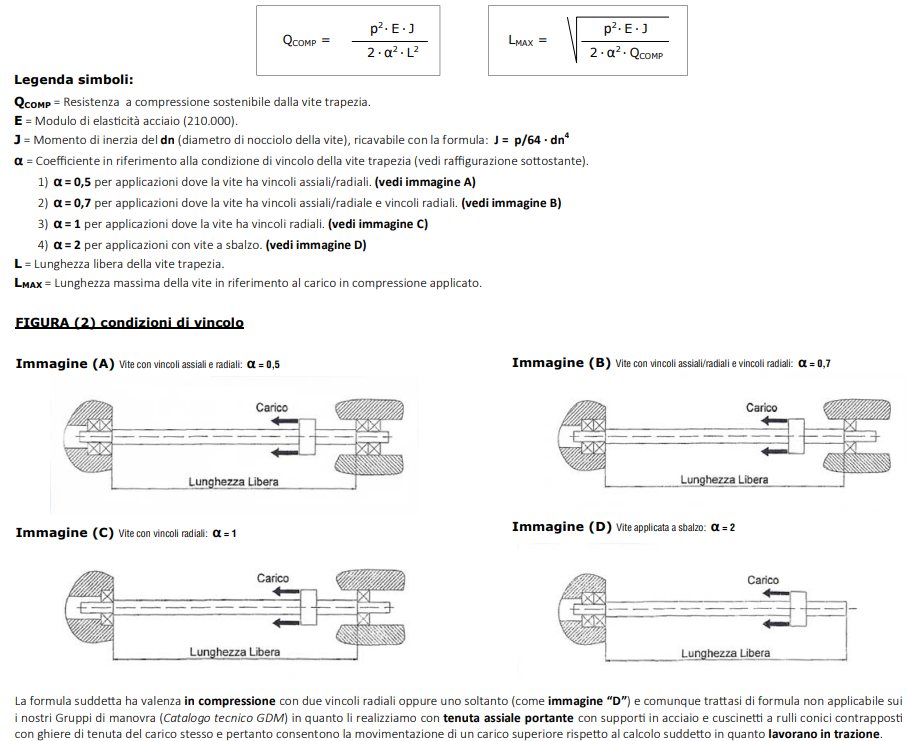
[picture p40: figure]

Carico Assiale Critico (Carico di Punta) Quando si è in presenza di viti caricate a compressione bisogna tener conto delle limitazioni dovute al “Carico di Punta”, per evitare che si verifichino flessioni della vite dovute all’eccessivo carico assiale di compressione. Il carico assiale dipende dal diametro di nocciolo della vite, dai vincoli alle estremità (cuscinetti) e dalla lunghezza libera.

[in mm]

## Caso A Vincoli Assiali + Radiali

Vite con vincoli assiali e radiali (α = 0,5)
La vite è vincolata sia assialmente che radialmente su entrambe le estremità. Questo vincolo impedisce sia gli spostamenti longitudinali che quelli trasversali, creando una condizione di incastro (ovviamente non nel senso di rotazione della vite. La lunghezza libera è massima e coincide con la distanza tra i supporti.
Comportamento sotto carico:
- Il coefficiente α = 0,5 indica la condizione più favorevole tra quelle mostrate, infatti essendo basso vuol dire che ho più resistenza alla compressione per cui ho meno flessione da parte della vite
- La lunghezza massima L_MAX sarà la più elevata per una data resistenza a compressione quindi potrà essere più lunga e piegarsi di meno
- Sotto carico di punta, la vite tenderà a instabilizzarsi
- I vincoli radiali impediscono rotazioni alle estremità, mantenendo tangenti parallele
- È la configurazione più stabile e resistente al carico di punta

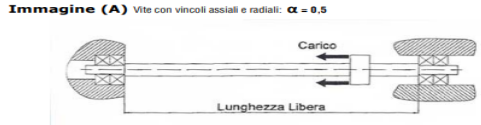
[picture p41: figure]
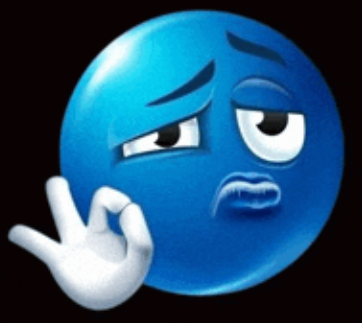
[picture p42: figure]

## Caso B Vincoli Radiali/Assiali + Radiali

Vite con vincoli assiali/radiali e vincoli radiali (α = 0,7)
Una estremità presenta vincoli sia assiali che radiali (incastro completo), mentre l'altra è vincolata solo radialmente (quindi può andare su e giù), permettendo lo scorrimento assiale. Questa è una condizione intermedia di vincolo.
Comportamento sotto carico:
- Il coefficiente α = 0,7 indica una condizione intermedia di stabilità
- La lunghezza massima L_MAX è inferiore rispetto all'immagine A perché il carico andando verso il centro piegherà semore di più la vite
- L'estremità con solo vincolo radiale può scorrere assialmente sotto carico
- La deformazione per instabilità sarà asimmetrica perché ovviamente ci sono vincoli diversi
Tendendo quindi a deformarsi di più verso destra (parte con meno vincoli)
- Maggiore tendenza all'inflessione rispetto alla configurazione A

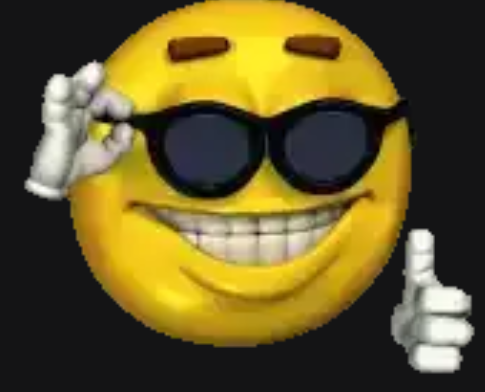
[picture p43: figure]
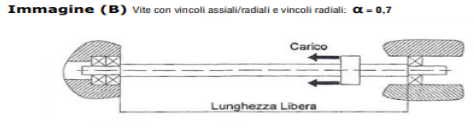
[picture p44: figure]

## Caso C Vincoli Radiali

Vite con soli vincoli radiali (α = 1)
Entrambe le estremità hanno solo vincoli radiali, permettendo il completo scorrimento assiale. La situa non va affatto bene
Comportamento sotto carico:
- Il coefficiente α = 1 rappresenta la condizione meno favorevole tra le prime tre
- La lunghezza massima L_MAX rispetto a prima è molto ridotta, non si potranno mettere delle viti molto lunghe, inizia a peggiorare molto
- La deformazione avverrà accentuata al centro della lunghezza libera
- Richiede maggiore attenzione nel dimensionamento perché tendera a diventare a banana
E comprometterà anche i cuscinetti sforzandoli continuamente (a carico)

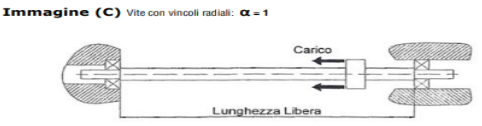
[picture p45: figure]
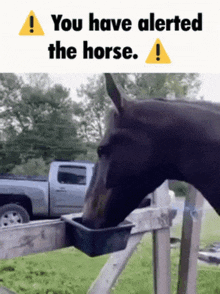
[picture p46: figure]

## Caso D vite a Sbalzo

Vite con soli vincoli radiali (α = 1)
La vite è incastrata da un solo lato e completamente libera dall'altro (mensola in compressione). Rappresenta la condizione più critica e sfavorevole dato che spesso e volentieri questo sitema tende a spezzare la vite e ad usurare rapidamente i cuscinetti.
Comportamento sotto carico:

Quindi fatelo poco spesso
o non fatelo proprio

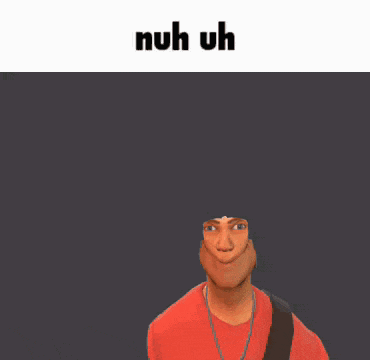
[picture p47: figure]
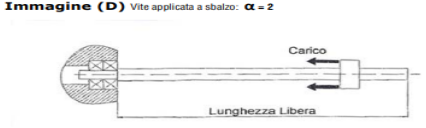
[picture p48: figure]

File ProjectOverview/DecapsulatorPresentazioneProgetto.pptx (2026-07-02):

## DECAPSULATOR


Automazione sostenibile per il riciclo del caffè

## Il team

- Pavanetto Riccardo
- Pisan Alessio
- Randazzo Manuel
- Dorigo Federico
- Poletti Christian
- Thanamcheril Arun James

## Che cos’è Decapsulator ?

- Decapsulator è un sistema automatico che separa il caffè dalla capsula, permettendo il recupero del materiale plastico e il riciclo del caffè.


## Perchè abbiamo scelto Decapsulator ?

- Abbiamo scelto di sviluppare Decapsulator perché le capsule di caffè sono un rifiuto molto diffuso e difficile da riciclare. L’idea del progetto è quella di separare automaticamente il caffè dalla capsula, rendendo possibile il recupero dei materiali e il loro corretto smaltimento. In questo modo abbiamo potuto applicare l’automazione e la meccatronica a un problema reale, unendo tecnologia e sostenibilità.


## I nostri obiettivi…


- I nostri obiettivi si sono concentrati nel:
- Realizzare un sistema automatico in grado di separare il caffè dalla capsula, riducendo l’intervento manuale dell’operatore.
- Migliorare la sicurezza, rendere il processo più efficiente e permettere il recupero dei materiali per il riciclo.
- Allo stesso tempo, applicare le competenze di meccatronica e automazione a un problema reale e attuale.


## RISULTATI E IMPATTO AMBIENTALE

- Il progetto decapsulator per noi non è solo un progetto di meccatronica, ma una soluzione concreta per ridurre l’impronta ecologica legata al consumo di caffè.
- - Efficienza di recupero: separazione netta tra cialda e caffè, facilitando il riciclo domestico.
- - Automazione sostenibile: l’utilizzo di componenti a basso consumo e sistemi automizzati riduce l’errore umano e otimizza i tempi di smaltimento.


## Primi processi del progetto


## Disegni tecnici, progetti 3D e prototipi


## Parte Elettronica


## Nuove Indroduzioni…


## Thanks for your attention !!

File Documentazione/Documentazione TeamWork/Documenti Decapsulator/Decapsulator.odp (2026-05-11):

## DECAPSULATOR


Automazione sostenibile per il riciclo del caffè

## Il team

- Pavanetto Riccardo
- Pisan Alessio
- Randazzo Manuel
- Dorigo Federico
- Poletti Christian
- Thanamcheril Arun James

## Che cos’è Decapsulator ?

- Decapsulator è un sistema automatico che separa il caffè dalla capsula, permettendo il recupero del materiale plastico e il riciclo del caffè.


## Perchè abbiamo scelto Decapsulator ?

- Abbiamo scelto di sviluppare Decapsulator perché le capsule di caffè sono un rifiuto molto diffuso e difficile da riciclare. L’idea del progetto è quella di separare automaticamente il caffè dalla capsula, rendendo possibile il recupero dei materiali e il loro corretto smaltimento. In questo modo abbiamo potuto applicare l’automazione e la meccatronica a un problema reale, unendo tecnologia e sostenibilità.


## I nostri obiettivi…


- I nostri obiettivi si sono concentrati nel:
- Realizzare un sistema automatico in grado di separare il caffè dalla capsula, riducendo l’intervento manuale dell’operatore.
- Migliorare la sicurezza, rendere il processo più efficiente e permettere il recupero dei materiali per il riciclo.
- Allo stesso tempo, applicare le competenze di meccatronica e automazione a un problema reale e attuale.


## RISULTATI E IMPATTO AMBIENTALE


- Il progetto decapsulator per noi non è solo un progetto di meccatronica, ma una soluzione concreta per ridurre l’impronta ecologica legata al consumo di caffè.
- - Efficienza di recupero: separazione netta tra cialda e caffè, facilitando il riciclo domestico.
- - Automazione sostenibile: l’utilizzo di componenti a basso consumo e sistemi automizzati riduce l’errore umano e otimizza i tempi di smaltimento.

## Primi processi del progetto


## Disegni tecnici, progetti 3D e prototipi


## Parte Elettronica


## Nuove Indroduzioni…


## Thanks for your attention !!



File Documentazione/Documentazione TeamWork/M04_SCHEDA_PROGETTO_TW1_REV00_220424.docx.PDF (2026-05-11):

(Rev.00-220424)
M04 | SCHEDA PROGETTO TW 1 | N. XXXX
| | (A cura del Soggetto Promotore)

ISTRUZIONI PER LA COMPILAZIONE: N.B. La compilazione deve essere effettuata solo per i Progetti del 1° anno di Team working. Trascrivere tutti i dati richiesti secondo le indicazioni riportate all’inizio di ogni tabella. In assenza del dato, lasciare il campo vuoto e non eliminare la tabella. Non spostare di pagina le tabelle e non modificare la formattazione del file originale fornito. Per qualsiasi ulteriore info contattare il Referente di Contest (ptobaldo@itsmeccatronico.it - 335 6765086 anche tramite whatsapp)
| 1- DATI IDENTIFICATIVI DEL TEAM
Sede | Montebelluna – Castelfranco Veneto
Cod. Corso
Studenti | Manuel Randazzo, Riccardo Pavanetto, Alessio Pisan, Federico Dorigo, Christian Poletti
Tutor | Maggisano Caterina
Coordinatore | Orsini Roberto
2- NOME DEL PROGETTO

## Decapsulator

3- UTILITÀ PER LA PERSONA E/O LA PRODUZIONE INDUSTRIALE

Specificare i benefici per la persona (Utilizzatore) e/o per l’industria anche rispetto ad eventuali prodotti simili presenti nel mercato
Il nostro macchinario è ideato per la suddivisione automatica delle cialde da caffè, suddivide l’involucro delle capsule in materiale plastico o alluminio dal contenuto interno in due contenitori distinti. Tramite un’operazione di punzonatura e successivamente di raschiatura della capsula possiamo così dividere il contenuto dall’involucro esterno. E’ stato pensato per facilitare l’operazione di smistamento che tramite l’impiego di questo macchinario verrà fatta in maniera accurata e automatica senza richiedere l’intervento dell’utente facendolo inoltre risparmiare del tempo da questa attività. Il materiale plastico o in alluminio verrà gettato direttamente sul contenitore adibito alla plastica per poi essere magari riutilizzato, mentre la polvere di caffè cadrà direttamente nel suo contenitore apposito. Una volta finito il processo l’utente potrà scegliere a suo piacimento cosa fare: per quanto riguarda la plastica potrà decidere di utilizzarla come riciclo o semplicemente gettarla sul bidone della plastica, invece riguardo alla polvere di caffè può decidere di gettarla sull’umido oppure se l’utente possiede delle piante o un piccolo orto sarà possibile utilizzarlo come ammendante per il terreno, portando al suolo una discreta quantità di azoto, inoltre può aumentare la biodiversità del suolo, migliora il drenaggio su suoli argillosi, fornisce materia organica, rende il suolo più acido, previene le malattie fungine e molti altri benefici.

© Fondazione ITS Academy Meccatronico Veneto 2024 – Tutti i diritti riservati – Riproduzione e trasmissione vietate (Riferirsi all’indicazione di protezione ISO 16016). La proprietà intellettuale dei progetti presentati, viene regolata dal “Regolamento sui brevetti e sulla proprietà intellettuale della Fondazione ITS Academy Meccatronico Veneto” e dalla legislazione vigente.

4- DESCRIZIONE DEL PROGETTO

Descrizione dettagliata dello scopo per cui è stato progettato e verrà realizzato il prototipo (Es. A cosa serve? A chi è destinato? In quale ambito può essere utilizzato? - Domestico, industriale - Ecc.). N.B. Lunghezza del testo Max. 1500 caratteri (spazi inclusi)

Il nostro prodotto di piccole dimensioni è stato pensato per uso domestico oppure per ufficio. Ideato per la suddivisione automatica delle cialde da caffè in due contenitori distinti, suddividendo l’involucro delle capsule in materiale plastico o alluminio dall’contenuto interno delle cialde. E’ stato pensato per facilitare l’operazione di smistamento che tramite l’impiego di questo macchinario verrà fatta in maniera accurata e automatica senza richiedere l’intervento dell’utente facendolo inoltre risparmiare del tempo da questa attività. Il macchinario automatizzato è composto da 5 macro aree:
1. Area stoccaggio capsule, un piccolo sistema di immaginamento verticale ideato per ospitare le cialde da suddividere.
2. Ralla multifunzione, ralla ideata per svolgere l’operazione di prelievo della cialda da caduta.
3. Meccanismo di punzonatura e raschiatura e di immagazzinamento cialde nei contenitori.
4. Contenitore per gli involucri delle cialde.
5. Contenitore per il contenuto interno delle cialde.

5- PRESENTAZIONE DEL PROGETTO

Inserire eventuali foto, immagini, schemi e/oi disegni esistenti che possono essere utili a comprendere meglio il progetto. N.B. La foto più “rappresentativa” del progetto dovrà essere caricata nella cartella in Drive (Materiale condiviso) denominata “Foto progetti e Team”


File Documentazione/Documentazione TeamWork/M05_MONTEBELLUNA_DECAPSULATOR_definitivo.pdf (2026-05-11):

© Fondazione ITS Academy Meccatronico Veneto 2024 – Tutti i diritti riservati – Riproduzione e trasmissione vietate (Riferirsi all’indicazione di protezione ISO 16016)
1
M05 | PROTOTIPO TW 2 | N. XXXX

Rev.00 - 100326
| 01- DATI IDENTIFICAZIONE TEAM
Sede | Montebelluna / Castelfranco
Cod. corso | 6131-0003-808-2024
Studenti | Dorigo Federico, Pavanetto Riccardo, Pisan Alessio, Randazzo Manuel, Poletti Christian, Thanamcheril Arun James
Tutor | Martinazzo Dino, Luisetto Loris, Tosatto Mirco, Falavigna Marco, Magisano Caterina, Silvestrin Giuseppe
Coordinatore | Orsini Roberto

### 02- DENOMINAZIONE DEL PROTOTIPO

## DECAPSULATOR

(Macchina per la separazione del caffè dal suo involucro)

### 03- DESCRIZIONE DEL PROTOTIPO

Questo dispositivo compatto, ideale per casa o ufficio, rivoluziona lo smaltimento delle capsule da caffè trasformandole da rifiuto complesso a risorsa. Il sistema automatizza la separazione tra involucro e contenuto tramite operazione di punzonatura e raschiatura, eliminando l'intervento manuale e garantendo precisione e risparmio di tempo.
Il macchinario si divide in 3 macro-aree:
- Inserimento e Stoccaggio cialde: magazzino verticale per le capsule da trattare;
- Ralla multifunzione: sistema di prelievo e gestione delle fasi di punzonatura, raschiatura ed espulsione;
- Stoccaggio dei due prodotti: due contenitori distinti per involucro e polvere di caffè.
Il cuore del progetto è la sostenibilità:
- Recupero materiali: plastica e alluminio, privi di residui organici, sono pronti per il riciclo industriale;
- Economia Circolare: il caffè residuo evolve in una risorsa biologica per il suolo. Agisce come nutriente azotato e ammendante organico, potenziando la biodiversità, la struttura drenante e la resilienza naturale del terreno.

Una soluzione concreta per rendere il rito del caffè un’azione realmente sostenibile e circolare.

2

04- TEST DI FUNZIONALITÀ | T= 3:00 (min) | Per ragioni logistiche e ambientali non favorevoli, è previsto il video
01) Inserimento manuale cialda in area di stoccaggio
02) Avvio del macchinario tramite touch nel display
03) Trasporto tramite tamburo da posizione inserimento a posizione di punzonatura e raschiatura
04) Punzonatura e raschiatura (separazione tra contenitore e caffè)
05) Trasporto in posizione di espulsione
06) Espulsione cialda e caffè in contenitori di raccolta
07) Trasporto tramite tamburo da posizione inserimento a posizione di punzonatura e raschiatura

### 05- DATI TECNICI

Larghezza / Lunghezza / Altezza | mm | 286 x 598 x 520
Massa | kg | 9,1
Il prototipo può essere esposto sopra un tavolo (Dim. ca.140x70 cm)? | | SI
Il prototipo deve essere appoggiato direttamente a terra? | | NO
Tensione alimentazione elettrica | VDC | 24
Potenza installata | kW | 0.084

### 06- TRASPORTO E MOVIMENTAZIONE

1) Con quale modalità viene trasportato e movimentato il prototipo: x Assemblato □ Smontato
3) Il prototipo o i suoi componenti, possono essere sollevati e movimentati manualmente?
□ NO x SI, da N. 1 Persona

N.B. La normativa di sicurezza sulla movimentazione manuale dei carichi prevede una massa Max. di

### 25 kg ad operatore

4) Il prototipo o i suoi componenti, devono essere movimentati mediante l’utilizzo di mezzi e accessori idonei al sollevamento? x NO □ SI (Specificare - Es. Carrello elevatore, catene, funi, ecc.)


3

### 07- PRESENTAZIONE DEL PROTOTIPO


4


5


6


7


8

9

### 08- COMPONENTI PRINCIPALI

N. | Denominazione | Funzione
1 | Motore del Tamburo | Movimento rotatorio del tamburo
2 | Servomotore Paratia | Sistema di cauta capsula
3 | Motore del Punzone | Movimento del Punzone
4 | Punzone | Foratura capsula
5 | Raschiatore | Pulizia involucro dal caffè
6 | Tamburo (ralla) | Guida della capsula nel ciclo
7 | Display | interfaccia uomo-macchina
8 | Data Storage | Salva i dati dell’ultimo stato del macchinario e dati utente
9 | Sensore presenza capsule | Segnala quando c’è la capsula
10 | Sensore caduta capsule | Segnala quando la cialda cade e se incastrata
11 | Contenitore Caffè | Contiene la polvere di caffè
12 | Contenitore Capsula | Contiene l’involucro
13 | Ventola | Ventola per raffreddare gli elementi elettronici interni

### 09 - MATERIALI UTILIZZATI

N. | Materiale | Proprietà e caratteristiche
1 | PETG | Polietilene ad alta resistività, usato per la componentistica principale non realizzabili con semplice tornitura e fresatura, scelto perché è un giusto compromesso tra resistenza meccanica, resistenza al calore e facilità di stampa
2 | Acciaio Inox | Ottima tenuta meccanica e lunga durata nel tempo, usato per la vite, per la movimentazione di punzonatura e raschiatura
3 | Alluminio | Usato per lo scheletro del macchinario, per la sua leggerezza e resistività
4 | Ottone | Utilizzato per la madre-vite per la movimentazione del sistema di punzonatura e raschiatura, scelto inoltre per il suo basso coefficiente di attrito
5 | Plexiglass | Usato per la protezione della parte di movimentazione della macchina, anche per la realizzazione del box per accogliere la scheda elettronica per pilotare la macchina

10

### 10 - TECNICHE DI LAVORAZIONE IMPIEGATE

Stampa 3D, Tornitura, Fresatura, Galvanizzazione elettrolitica, lavorazioni da banco (taglio, foratura, maschiatura, calettatura).

### 11- UTILITÀ PER LA PERSONA E/O LA PRODUZIONE INDUSTRIALE

Il prototipo è progettato per integrarsi perfettamente sia in contesti domestici che professionali, ponendosi come il cuore pulsante di una micro-economia circolare domestica, dove l'innovazione trasforma definitivamente il concetto di rifiuto in risorsa.

L’obiettivo primario è la gestione virtuosa del fine-vita delle capsule di caffè, garantendo una separazione dei materiali (alluminio, plastica e residuo organico) rapida, precisa e standardizzata.

Eliminando le barriere logistiche e i tempi onerosi che spesso scoraggiano la differenziazione manuale, il dispositivo trasforma un rifiuto complesso in una risorsa preziosa già pronta per il recupero. Questo processo non genera solo un valore ecologico, ma anche un beneficio economico tangibile per l'utente: la drastica riduzione del volume della frazione residua (secco indifferenziato) permette di ottimizzare i costi di smaltimento, favorendo il risparmio economico specialmente nei sistemi di gestione dei rifiuti basati su tariffazione puntuale.

In questo modo, l'utilizzatore non solo preserva una risorsa temporale preziosa, ma diventa protagonista di un modello di economia circolare. Il risultato è un abbattimento drastico dell'impronta ecologica legata al consumo quotidiano di caffè, coniugando responsabilità ambientale, praticità d'uso e convenienza economica.

11

### 12- CRITERI DI SOSTENIBILITÀ

La maggior parte del progetto è stato realizzato in PETG (Polietilene Tereftalato modificato con Glicole) è considerato un materiale moderatamente sostenibile per la stampa 3D, soprattutto perché è altamente riciclabile (spesso classificato col numero 1 o 7). Sebbene non sia biodegradabile, la sua riciclabilità e la disponibilità di versioni riciclate (e-PETG) lo rendono un'opzione ecologica rispetto ad altre plastiche.

Ecco i punti chiave sulla sostenibilità del PETG:

- Riciclabilità: Il PETG può essere riciclato, il che aiuta a ridurre i rifiuti plastici;
- Durata: Essendo un materiale durevole e resistente, il PETG è ideale per applicazioni funzionali a lungo termine, riducendo la necessità di sostituzioni frequenti;
- Differenza dal PLA: A differenza del PLA (che può essere compostabile industrialmente), il PETG è un polimero termoplastico, quindi non si biodegrada, ma offre una migliore riciclabilità in certi contesti;

### 13- CONFORMITÀ

### 5.1 Destinazione d’uso

Il presente apparato è un sistema elettromeccanico progettato per la separazione e il recupero selettivo dei residui di caffè da capsule esauste. Il processo avviene attraverso l'azione combinata di un tamburo rotante ad alta efficienza, un sistema di punzonatura meccanica per la perforazione degli involucri e un dispositivo di raschiamento per la rimozione pneumatico-meccanica dei fondi.

12

### 5.2 Direttive di Riferimento

Il progetto è stato sviluppato seguendo i criteri di sicurezza stabiliti dalle seguenti Direttive Europee:

- Direttiva Macchine 2006/42/CE: Per quanto riguarda la protezione dagli organi in movimento (tamburo e punzone) e i sistemi di interblocco;
- Direttiva Bassa Tensione (LVD) 2014/35/UE: Per la gestione della componentistica elettrica e dell'isolamento;
- Direttiva Compatibilità Elettromagnetica (EMC) 2014/30/UE: Per il contenimento dei disturbi elettromagnetici generati dal motore elettrico.

### 5.3 Norme Armonizzate Applicate (Principali)

Per la riduzione dei rischi sono state tenute in considerazione le seguenti norme tecniche:

- EN ISO 12100: Valutazione e riduzione del rischio;
- EN ISO 13857: Distanze di sicurezza per impedire il raggiungimento di zone pericolose con le mani;
- EN 60335-1: Sicurezza degli apparecchi elettrici d’uso domestico e similare.

### 5.4 Requisiti Essenziali di Sicurezza (RES) implementati

Ai fini della protezione dell'operatore, sono stati integrati i seguenti sistemi:

- Protezione Meccanica: Carter fisso che impedisce il contatto con il tamburo e il raschiatore durante il ciclo di lavoro;
- Protezione Elettrica: Alimentazione del sistema a 24V DC (Bassissima Tensione di Sicurezza – SELV);
- Sistema di Interblocco: Si suppone che in caso di messa in produzione vi è da considerare l’implementazione di sistema di sicurezza qualora venga aperto il pannello.

13

### 14- DOCUMENTAZIONE TECNICA

La seguente documentazione tecnica deve essere disponibile presso lo stand espositivo al MECC DAY e consultabile, su richiesta, dalla Commissione dei Referenti di sede:

Copie cartacee:

1) Assieme 3D del prototipo | 2) Distinta base a livelli valorizzata | 3) Manuale di istruzioni

Copia digitale installata su pc: Dossier Tecnico

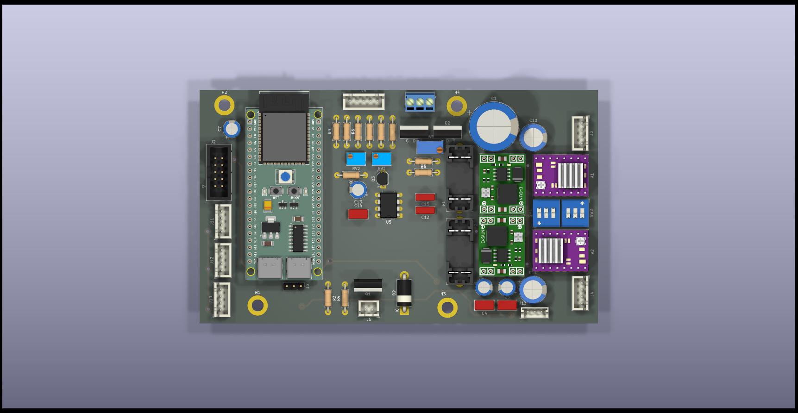
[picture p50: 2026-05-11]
Hardware/SCHEDA_PRINCIPALE/Scheda_principale_TRIDI2.jpg

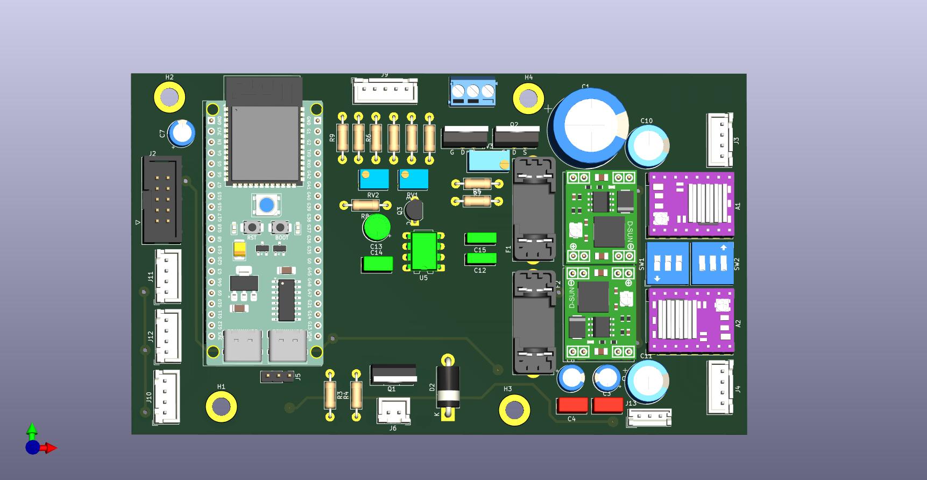
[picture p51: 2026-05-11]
Hardware/SCHEDA_PRINCIPALE/Scheda_principale.jpg

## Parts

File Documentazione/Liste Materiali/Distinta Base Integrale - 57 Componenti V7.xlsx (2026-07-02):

Livello 0 | Livello 1 | Livello 2 | Livello 3 | Livello 4 | CODICE ARTICOLO | DESCRIZIONE | FORNITORE | QUANTITÀ | PREZZO UNITARIO | TOTALE
MACCHINARIO |  |  |  |  |  | PROGETTO COMPLETO | INTERNO | 1
 | 761-3319 |  |  |  | 761-3319 | Profilo struttura RS PRO in Alluminio 40x40x1000mm | RS COMPONENTS | 1 | 1.219444444 | 1.219444444
 | 761-3313 |  |  |  | 761-3313 | Profilo struttura RS PRO in Alluminio 40x40x2000mm | RS COMPONENTS | 3 | 7.539583333 | 22.59097222
 | 767-5695 |  |  |  | 767-5695 | Staffa angolare RS PRO in Zinco pressofuso | RS COMPONENTS | 19 | 0.3083333333 | 5.441666667
 | 767-5761 |  |  |  | 767-5761 | Piastra di collegamento RS PRO in Acciaio | RS COMPONENTS | 5 | 0.2083333333 | 1.041666667
 | 32967553 |  |  |  | 32967553 | Copertura protettiva ebm-papst in Plastica | EBMPAPST | 1 | 0.2083333333 | 0.2083333333
 |  | 1606-23HS5628-8 |  |  | 1606-23HS5628-8 | Motore passo-passo bipolare NEMA 17 | futura elettronica | 2 | 1 | 2
 |  | 8218-DRV8825 |  |  | 8218-DRV8825 | Driver per motore passo-passo bipolare | futura elettronica | 2 | 0.4097222222 | 0.7916666667
 |  | 3302/20 100 SF |  |  | 3302/20 100 SF | Cavo piatto Passo 1.27 mm 20 poli | CONRAD | 1 | 0.1895833333 | 0.1895833333
 |  |  | 2850-HALLSENSOR |  | 2850-HALLSENSOR | sensori effetto hall | futura elettronica | 3 | 0.2013888889 | 0.5763888889
 |  |  |  | PHR-4 | PHR-4 | Morsettiera per cavo JST PHR 4 poli | CONRAD | 30 | 0.007638888889 | 0.1458333333
 |  |  |  | PHR-3 | PHR-3 | Morsettiera per cavo JST PHR 3 poli | CONRAD | 30 | 0.00625 | 0.1319444444
 |  |  |  | PHR-2 | PHR-2 | Morsettiera per cavo JST PHR 2 poli | CONRAD | 30 | 0.004861111111 | 0.09027777778
 |  |  |  | NDS-03-V | NDS-03-V | Interruttore DIP NDS-03-V | RS COMPONENTS | 5 | 0.05277777778 | 0.2638888889
 | SCH-01 |  |  |  | SCH-01 | Scheda controllo principale | INTERNO | 1
 | V-M4 |  |  |  | V-M4 | Viti M4 acciaio inox | ferramenta | 100 | 0.003472222222 | 0.2083333333
 | V-M8 |  |  |  | V-M8 | Viti M8 acciaio inox | ferramenta | 50 | 0.01041666667 | 0.3263888889
 | 761-3281 |  |  |  | 761-3281 | Piede articolato RS PRO M12 | RS COMPONENTS | 4 | 0.5347222222 | 2.083333333
 | 761-3290 |  |  |  | 761-3290 | Tappo terminale per profilo 40x40 | RS COMPONENTS | 10 | 0.05555555556 | 0.3333333333
 |  | MW-LRS-150-24 |  |  | MW-LRS-150-24 | Alimentatore switching 24V 150W | MEAN WELL | 1 | 0.9166666667 | 0.9166666667
 |  | 608-2RS |  |  | 608-2RS | Cuscinetto a sfere 8x22x7 | SKF | 8 | 0.1180555556 | 0.8333333333
 |  |  | GT2-BELT |  | GT2-BELT | Cinghia dentata GT2 6mm | fai-da-te | 5 | 0.125 | 0.625
 |  |  | GT2-PULLEY |  | GT2-PULLEY | Puleggia dentata 20 denti foro 5mm | fai-da-te | 4 | 0.2013888889 | 0.75
 | DADI-M4 |  |  |  | DADI-M4 | Dadi a martello per profilo cava 8 M4 | RS COMPONENTS | 100 | 0.008333333333 | 0.5
 | DADI-M8 |  |  |  | DADI-M8 | Dadi a martello per profilo cava 8 M8 | RS COMPONENTS | 50 | 0.0125 | 0.375
 | 32967552 |  |  |  | 32967552 | Griglia metallica per ventola 80mm | EBMPAPST | 1 | 0.1597222222 | 0.1597222222
 |  | CAVO-ALIM |  |  |  | CAVO-ALIM | Cavo alimentazione tripolare con spina | ferramenta | 1 | 0.25 | 0.25
 |  |  |  | XB2-BVB1 | XB2-BVB1 | Pulsante emergenza a fungo | SCHNEIDER | 1 | 0.625 | 0.625
 |  |  |  | LED-IND | LED-IND | Segnalatore LED 24V verde | ferramenta | 2 | 0.08333333333 | 0.1666666667
 | 767-5690 |  |  |  | 767-5690 | Vite testa cilindrica M8x16 | RS COMPONENTS | 50 | 0.01388888889 | 0.4166666667
 | 767-5691 |  |  |  | 767-5691 | Vite testa cilindrica M4x10 | RS COMPONENTS | 100 | 0.006944444444 | 0.4166666667
 |  | GUAINA-10 |  |  |  | GUAINA-10 | Guaina spiralata diametro 10mm | ferramenta | 5 | 0.05555555556 | 0.25
 |  | FASCETTE |  |  |  | FASCETTE | Set fascette nylon nere | ferramenta | 1 | 0.2083333333 | 0.2083333333
 | 761-3300 |  |  |  | 761-3300 | Angolare di rinforzo 40x80 | RS COMPONENTS | 4 | 0.4166666667 | 1.666666667
 |  |  | SEN-PROX |  | SEN-PROX | Sensore di prossimità induttivo M12 | RS COMPONENTS | 2 | 0.75 | 1.5
 |  |  |  | MORS-DIN | MORS-DIN | Morsettiere da guida DIN | PHOENIX | 10 | 0.07638888889 | 0.625
 |  | GUIDA-DIN |  |  |  | GUIDA-DIN | Guida DIN forata 200mm | ferramenta | 1 | 0.1666666667 | 0.1666666667
 | 32967556 |  |  |  | 32967556 | Ventola assiale 24V 80x80 | EBMPAPST | 1 | 0.75 | 0.75
 | 761-3320 |  |  |  | 761-3320 | Profilo alluminio 20x20x1000mm | RS COMPONENTS | 2 | 0.5 | 1
 | 767-5700 |  |  |  | 767-5700 | Staffetta 20x20 | RS COMPONENTS | 8 | 0.125 | 1
 |  |  |  | TERMO-1 | TERMO-1 | Guaina termorestringente set | ferramenta | 1 | 0.3333333333 | 0.3333333333
 | V-M5 |  |  |  | V-M5 | Viti M5 acciaio inox | ferramenta | 50 | 0.005555555556 | 0.1666666667
 | DADI-M5 |  |  |  | DADI-M5 | Dadi a martello M5 | RS COMPONENTS | 50 | 0.01041666667 | 0.3263888889
 |  | DIST-M3 |  |  |  | DIST-M3 | Distanziatori nylon M3 per PCB | ferramenta | 20 | 0.006944444444 | 0.08333333333
 |  |  | POT-10K |  | POT-10K | Potenziometro lineare 10k ohm | ferramenta | 1 | 0.1180555556 | 0.1180555556
 |  |  |  | MAN-1 | MAN-1 | Manopola per potenziometro | ferramenta | 1 | 0.04166666667 | 0.04166666667
 |  | USB-CABLE |  |  |  | USB-CABLE | Cavo USB micro per programmazione | ferramenta | 1 | 0.1666666667 | 0.1666666667
 | PLEXI-01 |  |  |  | PLEXI-01 | Pannello plexiglass 400x400x5mm | ferramenta | 1 | 1.041666667 | 1.041666667
 | PLEXI-02 |  |  |  | PLEXI-02 | Pannello plexiglass 200x400x5mm | ferramenta | 2 | 0.625 | 1.25
 | CERNIERA |  |  |  | CERNIERA | Cerniera plastica per profili | RS COMPONENTS | 2 | 0.2013888889 | 0.375
 |  |  |  | MANIGLIA | MANIGLIA | Maniglia in plastica per sportello | RS COMPONENTS | 1 | 0.2430555556 | 0.2430555556
 |  |  |  | CALAMITA | CALAMITA | Chiusura magnetica per sportello | ferramenta | 1 | 0.125 | 0.125
 | 761-3350 |  |  |  | 761-3350 | Canalina passacavi 25x25 | RS COMPONENTS | 2 | 0.2916666667 | 0.5833333333
 |  | MORSETTO-2 |  |  |  | MORSETTO-2 | Morsetto a vite 2 poli PCB | ferramenta | 10 | 0.03472222222 | 0.2083333333
 |  | MORSETTO-3 |  |  |  | MORSETTO-3 | Morsetto a vite 3 poli PCB | ferramenta | 5 | 0.04861111111 | 0.1597222222
 |  |  | RELAY-24 |  |  |  | RELAY-24 | Modulo relè 24V | ferramenta | 2 | 0.2847222222 | 0.5416666667
 | ETICHETTE |  |  |  | ETICHETTE | Set etichette identificazione cavi | ferramenta | 1 | 0.4166666667 | 0.4166666667
 | IMBALLO |  |  |  | IMBALLO | Cassa in legno per trasporto | interno | 1 | 2.083333333 | 2.083333333

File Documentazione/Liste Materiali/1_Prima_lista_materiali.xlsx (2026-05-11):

MATERIALE ELETTRICO
nome prodotto: | Produttore: | codice prodotto: | link prodotto | descrizione | prezzo (+iva) | quantità: | prezzo tot.
sensori effetto hall | futura elettronica | 2850-HALLSENSOR | Scheda con sensore effetto Hall 49E (https://futuranet.it/prodotto/scheda-con-sensore-hall-49e/) | Sensore effetto Hall per ralla e homing tramite uno spillo | 4.50 € | 3 | 13.50 € | inclusa
Motore passo-passo bipolare | futura elettronica | 1606-23HS5628-8 | Motore passo-passo bipolare NEMA 17 – 2,5 A (https://futuranet.it/prodotto/motore-passo-passo-bipolare-nema-17-25-a/) | Motore passo-passo bipolare NEMA 17 – 2,5 A | 24.00 € | 2 | 48.00 € | inclusa
Driver per motore passo-passo | futura elettronica | 8218-DRV8825 | https://futuranet.it/prodotto/driver-per-motore-passo-passo-bipolare-22a/ | Driver per motore passo-passo bipolare 2,2A per bobina, 45V max logica 3,3V-5,5V | 9.50 € | 2 | 19.00 € | inclusa
Scheda elettronica per Cella di carico - HX711 | futura elettronica | 3085-HX711BOARD | https://futuranet.it/prodotto/scheda-elettronica-per-cella-di-carico-hx711/ | Scheda elettronica basata sul chip HX711, un convertitore analogico-digitale a 24 bit, specifico per interfacciare la cella di carico, due celle collegabili (2 canali). Amplificatori di segnali individuali per singolo canale | 5.00 € | 1 | 5.00 € | inclusa
Cella di carico 1 kg | futura elettronica | 1606-1KGLOADCELL | cella di carico 1kg (https://futuranet.it/prodotto/cella-di-carico-1-kg/) | Cella di carico per misurare la quantità di caffè e di capsule all'interno del macchianario | 7.00 € | 2 | 14.00 € | inclusa
Ventola 24 Vdc 80x80x25 mm | futura elettronica | 6600-BSS24 | https://futuranet.it/prodotto/ventola-sunon-24-vdc-80x80x25/ | Ventola brushless d'ingresso e uscita per l'aria per il raffreddamento e il ricircolo del macchianario | 9.50 € | 2 | 19.00 € | inclusa
Arduino Shield TFT touch screen 3.5" | futura elettronica | 2850-3.5INCHSHIELD | https://futuranet.it/prodotto/arduino-shield-tft-touch-screen-3-5/ | Display touch per HMI modalità SPI max 40MHz | 32.00 € | 1 | 32.00 € | inclusa
Modulo DC-DC Step-Down regolabile 4,5-28 volt 3A | futura elettronica | 3085-MP1584ADJ | https://futuranet.it/prodotto/modulo-dc-dc-stepdown-regolabile-45-28-volt-3a/ | Step-down per microchip | 2.50 € | 1 | 2.50 € | inclusa
Staffa per motori passo-passo NEMA17 | futura elettronica | 2846-SMXNEMA17 | https://futuranet.it/prodotto/staffa-per-motori-passo-passo-nema17/ | staffa per nema 17 | 3.50 € | 1 | 3.50 € | inclusa
MATERIALE MECCANICO
nome prodotto: | Produttore: | codice prodotto: | link prodotto | descrizione | prezzo (+iva) | quantità | prezzo tot.
cuscinetto sferico | RS Italia | CODICE RS: 750-8703 | UC204 | Cuscinetto sferico, RS PRO, Ø interno 20mm, Ø esterno 47mm, carico statico 630kgf, in Acciaio | RS (https://it.rs-online.com/web/p/cuscinetti-ad-inserto/7508703) | Cuscinetto sferico, RS PRO, Ø interno 20mm, Ø esterno 47mm, carico statico 630kgf, in Acciaio | 12.53 € | 1.00 | 12.53 | esclusa
cuscinetto sferico radiale | RS Italia | CODICE RS: 286-7849 | 626-2Z | Cuscinetto a sfera Cuscinetti radiali a una corona di sfere SKF in Acciaio, Ø int. 6mm, Ø est. 19mm, Largh. guida 6mm | RS (https://it.rs-online.com/web/p/cuscinetti-a-sfera/2867849?gb=s) | Cuscinetto a sfera Cuscinetti radiali a una corona di sfere SKF in Acciaio, Ø int. 6mm, Ø est. 19mm, Largh. guida 6mm | 5.59 € | 1.00 | 5.59 € | esclusa
 |  |  |  |  |  |  |  |  | Rimanente | Rimanente finale
 |  |  |  |  |  | TOTALE | 174.62 € |  | €1200.00 | €1025.38
 |  |  |  |  |  |  |  |  | totale ordine
 |  |  |  |  |  |  |  |  | €174.62

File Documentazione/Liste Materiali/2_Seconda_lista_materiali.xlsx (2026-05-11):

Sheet: DISTINTA
GRUPPO TW | 1 | REFERENTE ACQUISTI | Dorigo Federico |  |  | COORDINATORE | Orsini Roberto
SEDE | MTB | INDIRIZZO SEDE | via J. Sansovino 6 Montebelluna (TV) |  |  | CODICE PROGETTO |  | 6131 3 808 2024
N° ORDINE | 2
NUMERO ARTICOLO | DESCRIZIONE |  |  | CODICE ARTICOLO FORNITORE | FORNITORE | N° PEZZI | PREZZO PER UNITA' (IVA ESCLUSA) | TOTALE (IVA ESCLUSA) | NOTE ( ES. MISURE - COLORE - TAGLIO )
1 | Vite trapezoidale da 8mm p2mm 500mm con chiocciola |  |  | 26846-VITET8P2-500 | FUTURA ELETTRONICA (FUTURA GROUP) | 1 | €12.00 | €12.00 | Arrivato
2 | Servo analogico con ingranaggi in metallo e completo di accessori. Alimentazione: da 4,8 VDC a 6 VDC, coppia di torsione: 9,4 kg•cm (4.8V) – 11 kg•cm (6V), angolo di rotazione: 360°, velocità a 4,8V: 0,19 secondi/60° senza carico, velocità a 6V: 0,15 secondi/60° senza carico. Dimensioni (mm): 42,7×40,9×20, peso: 55 grammi, temperatura di funzionamento: da 0°C a +60°C. |  |  | 1606-MG996R | FUTURA ELETTRONICA (FUTURA GROUP) | 1 | €9.00 | €9.00 | Arrivato
3 | Motore passo-passo bipolare NEMA 17 – 2,5 A |  |  | 7300-STEPMOT3DRAG | FUTURA ELETTRONICA (FUTURA GROUP) | 1 | €24.00 | €24.00 | Arrivato
4 | Servo motore 9.4kg/cm ingranaggi metallo 360° |  |  | 1606-MG996R | FUTURA ELETTRONICA (FUTURA GROUP) | 1 | €9.00 | €9.00 | Arrivato
5 | Vite trapezoidale da 8mm p2mm 500mm con chiocciola |  |  | 26846-VITET8P2-501 | FUTURA ELETTRONICA (FUTURA GROUP) | 1 | €15.00 | €15.00 | Arrivato
6 |  |  |  |  |  |  |  | €0.00
7 |  |  |  |  |  |  |  | €0.00 |  | Rimanente | Rimanente finale
8 |  |  |  |  |  |  |  | €0.00 |  | €1025.38 | €956.38
9 |  |  |  |  |  |  |  | €0.00
10 |  |  |  |  |  |  |  | €0.00 |  | totale ordine
11 |  |  |  |  |  |  |  | €0.00 |  | €69.00
12 |  |  |  |  |  |  |  | €0.00
13 |  |  |  |  |  |  |  | €0.00
14 |  |  |  |  |  |  |  | €0.00
15 |  |  |  |  |  |  |  | €0.00
16 |  |  |  |  |  |  |  | €0.00
17 |  |  |  |  |  |  |  | €0.00
18 |  |  |  |  |  |  |  | €0.00
19 |  |  |  |  |  |  |  | €0.00
20 |  |  |  |  |  |  |  | €0.00
21 |  |  |  |  |  |  |  | €0.00
22 |  |  |  |  |  |  |  | €0.00
23 |  |  |  |  |  |  |  | €0.00
24 |  |  |  |  |  |  |  | €0.00
25 |  |  |  |  |  |  |  | €0.00
26 |  |  |  |  |  |  |  | €0.00
27 |  |  |  |  |  |  |  | €0.00
28 |  |  |  |  |  |  |  | €0.00
29 |  |  |  |  |  |  |  | €0.00
30 |  |  |  |  |  |  |  | €0.00
31 |  |  |  |  |  |  |  | €0.00
32 |  |  |  |  |  |  |  | €0.00
33 |  |  |  |  |  |  |  | €0.00
34 |  |  |  |  |  |  |  | €0.00
35 |  |  |  |  |  |  |  | €0.00
36 |  |  |  |  |  |  |  | €0.00
37 |  |  |  |  |  |  |  | €0.00
38 |  |  |  |  |  |  |  | €0.00
39 |  |  |  |  |  |  |  | €0.00
 |  |  |  |  |  |  | TOTALE | €69.00

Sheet: UFF. ACQ
Riservato ITS - UFFICIO ACQUISTI
Ordinato il: | Note
Consegnato il:
Ordine evaso:
Fornitore
Rif. Ordine
N° ordine
Cons. Prev.
Rif. Ddt

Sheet: DATI
NUMERO ORDINE | CODICE REGIONALE | SEDE | TITOLO SINTETICO | COORDINATORE | FORNITORE
1 | 6131-0001-1032-2023 | Vicenza | AUTOMAZIONE SIST. MECCATRONICI | PORTINARI SERGIO | RS COMPONENTS
2 | 6131-0002-1032-2023 | Padova | AUTOMAZIONE SIST. MECCATRONICI | CONSOLARO DANIELE | FUTURA ELETTRONICA (FUTURA GROUP)
3 | 6131-0003-1032-2023 | Verona | AUTOMAZIONE SIST. MECCATRONICI | FEDELE DI MARCO | ROBOT ITALY
4 | 6131-0004-1032-2023 | Montebelluna | AUTOMAZIONE SIST. MECCATRONICI | ORSINI ROBERTO | DISTRELEC
5 | 6131-0005-1032-2023 | Mestre-VE | AUTOMAZIONE SIST. MECCATRONICI | GAROFALO ANTONIO | MICROBOT DI PROSSEDA MIRKO
6 | 6131-0006-1032-2023 | Conegliano SINISTRA PIAVE | AUTOMAZIONE SIST. MECCATRONICI | VENDRAMINI CHRISTIAN | LEROY MERLIN
7 | 6131-0007-1032-2023 | Belluno | AUTOMAZIONE SIST. MECCATRONICI | ZANCANARO MICHELE | FERRAMENTA NEGRIN
8 | 6131-0008-1032-2023 | Treviso | INNOVAZIONE DI PROCESSI E PRODOTTI MECCANICI | BONSO TIZIANO | CONRAD
9 | 6131-0009-1032-2023 | Schio | INNOVAZIONE DI PROCESSI E PRODOTTI MECCANICI | MAINO GIAMPAOLO | LASER IDEA SRL
10 | 6131-0010-1032-2023 | Vicenza | INDUSTRIA 4.0 | SGROI ANDREA | Arkengraf Srl - PlexyFaiDaTe
11 | 6131-0011-1032-2023 | Padova | INNOVAZIONE DI PROCESSI E PRODOTTI MECCANICI | VINANTE LEONARDO | MARCHIOL SPA
12 | 6131-0012-1032-2023 | Thiene | INDUSTRIA 4.0 | FRIGO GUIDO | FERRAMENTA ZORZETTO
13 | 6131-0013-1032-2023 | Portogruaro | AUTOMAZIONE SIST. MECCATRONICI | TOMMASI MASSIMILIANO
14 | 6131-0014-1032-2023 | Schio | AUTOMAZIONE SIST. MECCATRONICI | GASPANI GIANCARLO
15 | 6131-0015-1032-2023 | Bassano del Grappa | AUTOMAZIONE SIST. MECCATRONICI | FIORESE VLADIMIRO
16 | 6131-0016-1032-2023 | Este PD (PADOVA SUD) | AUTOMAZIONE SIST. MECCATRONICI | TONIOLO LILIANA

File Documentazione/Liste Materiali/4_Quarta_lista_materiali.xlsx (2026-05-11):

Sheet: DISTINTA
GRUPPO TW | 1 | REFERENTE ACQUISTI | Dorigo Federico |  |  | COORDINATORE | Orsini Roberto
SEDE | MTB | INDIRIZZO SEDE | via J. Sansovino 6 Montebelluna (TV) |  |  | CODICE PROGETTO |  | 6131 3 808 2024
N° ORDINE | 4
NUMERO ARTICOLO | DESCRIZIONE |  |  | CODICE ARTICOLO FORNITORE | FORNITORE | N° PEZZI | PREZZO PER UNITA' (IVA ESCLUSA) | TOTALE (IVA ESCLUSA) | NOTE ( ES. MISURE - COLORE - TAGLIO )
1 | Giunto in alluminio 5 mm – 8 mm |  |  | 8300-HUB5MM8 | FUTURA ELETTRONICA (FUTURA GROUP) | 3 | €1.48 | €4.44
2 | Interruttore DIP NDS-03-V, SPST, 25 mA, 3 posizioni, attuatore a Rialzato, Foro passante |  |  | NDS-03-V | RS COMPONENTS | 1 | €5.80 | €5.80 | È 1 sacchetto da 5 componenti
3 | Copertura protettiva ebm-papst in Plastica, 80 x 80mm, ventola da 80mm |  |  | 92162-2-2929 | RS COMPONENTS | 2 | €3.80 | €7.60 | 9.27
4 | Raspberry Pi 5 versione con 16 GB di memoria |  |  | 7310-RPI5-16GB | FUTURA ELETTRONICA (FUTURA GROUP) | 1 | €144.30 | €144.30
5 | Servo motore 10.5kg/cm ingranaggi metallo 180° |  |  | 8300-MG946R | FUTURA ELETTRONICA (FUTURA GROUP) | 1 | €6.63 | €6.63
6 | Intenso High Performance Scheda microSDHC 8 GB Class 10 incl. Adattatore S |  |  | 3413460 | CONRAD | 1 | €3.50 | €3.50
7 | Kingston Canvas Select Plus Scheda microSDXC 128 GB Class 10 UHS-I |  |  | SDCS2/128GBSP | CONRAD | 1 | €8.57 | €8.57 |  | Rimanente | Rimanente finale
8 | SanDisk microSDXC Ultra 64GB (A1/UHS-I/Cl.10/140MB/s) + Adapter "Mobile" Scheda microSDXC 64 GB A1 Application Performan |  |  | SDSQUAB-064G-GN6MA | CONRAD | 1 | €7.01 | €7.01 |  | €646.52 | €256.92
10 | Angolare 90° in alluminio pressofuso |  |  | 7350-ANG90ALLU | FUTURA ELETTRONICA (FUTURA GROUP) | 30 | €0.50 | €15.00
11 | Cramolin GRAPHIT 1281411 Lacca 200 ml |  |  | 820571-62 | CONRAD | 1 | €22.99 | €22.99 |  | totale ordine
12 | Filamento per stampante 3D NANOVIA, PET-G, Nero, diam. 1.75mm |  |  | 635-147 | RS COMPONENTS | 2 | €21.75 | €43.50 | 53.07 | €389.60
13 | 10 dischi magnetici 8x3 mm |  |  |  | FUTURA ELETTRONICA (FUTURA GROUP) | 2 | €6.00 | €12.00
15 | Diodo DiodesZetex, Foro passante, 10 A, 100 V, TO-220, Bassa dispersione, 3 Pin |  |  | 8220-MAGNET5 | RS COMPONENTS | 1 | €2.92 | €2.92 | è una confezione da 10, quindi solo 1 confezione
17 | Contatto a crimpare JST PH Totale poli 1 BPH-002T-P0.5S 1 pz. |  |  | BPH-002T-P0.5S | CONRAD | 50 | €0.05 | €2.34 | l’ordine minimo è di 50, quindi è l’ordine minimo
18 | Connettore maschio da incasso (standard) JST PH Totale poli 8 Passo: 2 mm S8B-PH-SM4-TB (LF)(SN) 1 pz. |  |  | S8B-PH-SM4-TB (LF)(SN) | CONRAD | 5 | €1.01 | €5.03 | è una confezione da 5, quindi solo 1 confezione
19 | Connettore maschio da incasso (standard) JST PH Totale poli 4 Passo: 2 mm S4B-PH-SM4-TB (LF)(SN) 1 pz. |  |  | S4B-PH-SM4-TB (LF)(SN) | CONRAD | 7 | €0.28 | €1.96 | è una confezione da 7, quindi solo 1 confezione
20 | Connettore maschio da incasso (standard) JST PH Totale poli 3 Passo: 2 mm S3B-PH-SM4-TB (LF)(SN) 1 pz. |  |  | S3B-PH-SM4-TB (LF)(SN) | CONRAD | 7 | €0.44 | €3.11 | è una confezione da 7, quindi solo 1 confezione
21 | Connettore maschio da incasso (standard) JST PH Totale poli 2 Passo: 2 mm S2B-PH-SM4-TB (LF)(SN) 1 pz. |  |  | S2B-PH-SM4-TB (LF)(SN) | CONRAD | 10 | €0.40 | €4.00 | è una confezione da 10, quindi solo 1 confezione
22 | Fischer Elektronik Connettore maschio (standard) Numero di righe: 1 Poli per fila: 20 SL LP 5 SMD 051/ 20/S 1 pz. |  |  | SL LP 5 SMD 051/ 20/S | CONRAD | 10 | €0.63 | €6.32
23 | Portabatterie 9V PP3, montaggio PCB, contatti Montaggio su circuito stampato |  |  | 185-4728 | RS COMPONENTS | 1 | €2.09 | €2.09
24 | Batteria 9V RS PRO, 1.2Ah, Litio diossido di manganese |  |  | 784-5992 | RS COMPONENTS | 1 | €12.21 | €12.21
25 | Condensatore RS PRO, 4700μF, 35V cc, ±20%, 105°C, Radiale, Foro passante |  |  | 711-1374 | RS COMPONENTS | 2 | €1.04 | €2.08 | è una confezione da 2, quindi solo 1 confezione
26 | Condensatore RS PRO, 470μF, 35V cc, ±20%, 105°C, Radiale, Foro passante |  |  | 711-1299 | RS COMPONENTS | 10 | €0.42 | €4.17 | è una confezione da 10, quindi solo 1 confezione
29 | Potenziometro trimmer Bourns, 5kΩ, 12 giri, Regolazione dall'alto, Su foro |  |  | 769-2243 | RS COMPONENTS | 4 | €1.88 | €7.52
30 | Adattatore AC/DC RS PRO 24V cc, 3A, spina IEC 320 C14 |  |  | 204-7566 | RS COMPONENTS | 1 | €30.37 | €30.37
31 | Presa DC da pannello 5,5 x 2,1 mm |  |  | 1606-DCPLUG | FUTURA ELETTRONICA (FUTURA GROUP) | 4 | €0.78 | €3.12
32 | Case per Raspberry Pi Raspberry Pi ABS serie Pi Case, per Raspberry Pi 5 Nero |  |  | 219-256 | RS COMPONENTS | 1 | €9.34 | €9.34
33 | Alimentatore per Raspberry Pi Raspberry Pi, presa USB di tipo C con Connettore maschio EU, cavo da 1.2m |  |  | 219-261 | RS COMPONENTS | 1 | €11.68 | €11.68
 |  |  |  |  |  |  |  | €0.00
 |  |  |  |  |  |  |  | €0.00
34 |  |  |  |  |  |  |  | €0.00
35 |  |  |  |  |  |  |  | €0.00
36 |  |  |  |  |  |  |  | €0.00
37 |  |  |  |  |  |  |  | €0.00
38 |  |  |  |  |  |  |  | €0.00
39 |  |  |  |  |  |  |  | €0.00
40 |  |  |  |  |  |  |  | €0.00
 |  |  |  |  |  |  | TOTALE | €389.60

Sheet: UFF. ACQ
Riservato ITS - UFFICIO ACQUISTI
Ordinato il: | Note
Consegnato il:
Ordine evaso:
Fornitore
Rif. Ordine
N° ordine
Cons. Prev.
Rif. Ddt

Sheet: DATI
NUMERO ORDINE | CODICE REGIONALE | SEDE | TITOLO SINTETICO | COORDINATORE | FORNITORE
1 | 6131-0001-1032-2023 | Vicenza | AUTOMAZIONE SIST. MECCATRONICI | PORTINARI SERGIO | RS COMPONENTS
2 | 6131-0002-1032-2023 | Padova | AUTOMAZIONE SIST. MECCATRONICI | CONSOLARO DANIELE | FUTURA ELETTRONICA (FUTURA GROUP)
3 | 6131-0003-1032-2023 | Verona | AUTOMAZIONE SIST. MECCATRONICI | FEDELE DI MARCO | ROBOT ITALY
4 | 6131-0004-1032-2023 | Montebelluna | AUTOMAZIONE SIST. MECCATRONICI | ORSINI ROBERTO | DISTRELEC
5 | 6131-0005-1032-2023 | Mestre-VE | AUTOMAZIONE SIST. MECCATRONICI | GAROFALO ANTONIO | MICROBOT DI PROSSEDA MIRKO
6 | 6131-0006-1032-2023 | Conegliano SINISTRA PIAVE | AUTOMAZIONE SIST. MECCATRONICI | VENDRAMINI CHRISTIAN | LEROY MERLIN
7 | 6131-0007-1032-2023 | Belluno | AUTOMAZIONE SIST. MECCATRONICI | ZANCANARO MICHELE | FERRAMENTA NEGRIN
8 | 6131-0008-1032-2023 | Treviso | INNOVAZIONE DI PROCESSI E PRODOTTI MECCANICI | BONSO TIZIANO | CONRAD
9 | 6131-0009-1032-2023 | Schio | INNOVAZIONE DI PROCESSI E PRODOTTI MECCANICI | MAINO GIAMPAOLO | LASER IDEA SRL
10 | 6131-0010-1032-2023 | Vicenza | INDUSTRIA 4.0 | SGROI ANDREA | Arkengraf Srl - PlexyFaiDaTe
11 | 6131-0011-1032-2023 | Padova | INNOVAZIONE DI PROCESSI E PRODOTTI MECCANICI | VINANTE LEONARDO | MARCHIOL SPA
12 | 6131-0012-1032-2023 | Thiene | INDUSTRIA 4.0 | FRIGO GUIDO | FERRAMENTA ZORZETTO
13 | 6131-0013-1032-2023 | Portogruaro | AUTOMAZIONE SIST. MECCATRONICI | TOMMASI MASSIMILIANO
14 | 6131-0014-1032-2023 | Schio | AUTOMAZIONE SIST. MECCATRONICI | GASPANI GIANCARLO
15 | 6131-0015-1032-2023 | Bassano del Grappa | AUTOMAZIONE SIST. MECCATRONICI | FIORESE VLADIMIRO
16 | 6131-0016-1032-2023 | Este PD (PADOVA SUD) | AUTOMAZIONE SIST. MECCATRONICI | TONIOLO LILIANA

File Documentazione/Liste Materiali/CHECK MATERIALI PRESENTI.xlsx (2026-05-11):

GRUPPO TW | 1 |  | REFERENTE ACQUISTI | Dorigo Federico |  |  | COORDINATORE | Orsini Roberto
SEDE | MTB |  | INDIRIZZO SEDE | via J. Sansovino 6 Montebelluna (TV) |  |  | CODICE PROGETTO |  | 6131 3 808 2024
N° ORDINE | -
NUMERO ARTICOLO | DESCRIZIONE |  |  |  | CODICE ARTICOLO FORNITORE | FORNITORE | N° PEZZI | PREZZO PER UNITA' (IVA ESCLUSA) | TOTALE (IVA ESCLUSA) | NOTE ( ES. MISURE - COLORE - TAGLIO )
1 | sensori effetto hall |  |  |  | 2850-HALLSENSOR | futura elettronica | 3 | 4.50 € | 13.50 € | Sensore effetto Hall per ralla e homing tramite uno spillo
2 | Motore passo-passo bipolare |  |  |  | 1606-23HS5628-8 | futura elettronica | 2 | 29.00 € | 48.00€ | Motore passo-passo bipolare NEMA 17 – 2,5 A
3 | Driver per motore passo-passo |  |  |  | 8218-DRV8825 | futura elettronica | 2 | 9.50€ | 19.00 € | Driver per motore passo-passo bipolare 2,2A per bobina, 45V max logica 3,3V-5,5V
4 | Scheda elettronica per Cella di carico - HX711 |  |  |  | 3085-HX711BOARD | futura elettronica | 1 | 5.00 € | 5.00 € | Scheda elettronica basata sul chip HX711, un convertitore analogico-digitale a 24 bit, specifico per interfacciare la cella di carico, due celle collegabili (2 canali). Amplificatori di segnali individuali per singolo canale
5 | Cella di carico 1 kg |  |  |  | 1606-1KGLOADCELL | futura elettronica | 2 | 7.00€ | 14.00€ | Cella di carico per misurare la quantità di caffè e di capsule all'interno del macchianario
6 | Ventola 24 Vdc 80x80x25 mm |  |  |  | 6600-BSS24 | futura elettronica | 2 | 9.50€ | 19.00€ | Ventola brushless d'ingresso e uscita per l'aria per il raffreddamento e il ricircolo del macchianario
7 | Arduino Shield TFT touch screen 3.5" |  |  |  | 2850-3.5INCHSHIELD | futura elettronica | 1 | 32.00€ | 32.00€ | Display touch per HMI modalità SPI max 40MHz
8 | Modulo DC-DC Step-Down regolabile 4,5-28 volt 3A |  |  |  | 3085-MP1584ADJ | futura elettronica | 1 | 2.50€ | 2.50 € | Step-down per microchip
9 | Staffa per motori passo-passo NEMA17 |  |  |  | 2846-SMXNEMA17 | futura elettronica | 1 | 3.50 € | 3.50 € | staffa per nema 17
10 | cuscinetto sferico |  |  |  | 750-8703 | RS Italia | 1 | 12.53€ | 12.53€ | Cuscinetto sferico, RS PRO, Ø interno 20mm, Ø esterno 47mm, carico statico 630kgf, in Acciaio
11 | cuscinetto sferico radiale |  |  |  | 286-7849 | RS Italia | 1 | 5.59 € | 5.59 € | Cuscinetto a sfera Cuscinetti radiali a una corona di sfere SKF in Acciaio, Ø int. 6mm, Ø est. 19mm, Largh. guida 6mm
12 | Vite trapezoidale da 8mm p2mm 500mm con chiocciola |  |  |  | 26846-VITET8P2-500 | futura elettronica | 1 | €12.00 | €12.00 | Arrivato
13 | Servo analogico con ingranaggi in metallo e completo di accessori. Alimentazione: da 4,8 VDC a 6 VDC, coppia di torsione: 9,4 kg•cm (4.8V) – 11 kg•cm (6V), angolo di rotazione: 360°, velocità a 4,8V: 0,19 secondi/60° senza carico, velocità a 6V: 0,15 secondi/60° senza carico. Dimensioni (mm): 42,7×40,9×20, peso: 55 grammi, temperatura di funzionamento: da 0°C a +60°C. |  |  |  | 1606-MG996R | futura elettronica | 2 | €9.00 | €18.00 | Arrivato
14 | Motore passo-passo bipolare NEMA 17 – 2,5 A |  |  |  | 7300-STEPMOT3DRAG | futura elettronica | 1 | €24.00 | €24.00 | Arrivato
15 | Servo motore 9.4kg/cm ingranaggi metallo 360° |  |  |  | 1606-MG996R | futura elettronica | 1 | €9.00 | €9.00 | Arrivato
16 | Profilo struttura RS PRO in Alluminio, Anodizzato, 30 x 30 mm x 2m |  |  |  | 264-7863 | RS COMPONENTS | 2 | €34.30 | €68.60 | 83.7
17 | Cuscinetto a sfera Cuscinetti radiali a una corona di sfere SKF in Acciaio, Ø int. 6mm, Ø est. 19mm, Largh. guida 6mm |  |  |  | 751-455 | RS COMPONENTS | 4 | €6.33 | €25.32
18 | Cuscinetto flangiato, Igus RJUM-06-12, Ø interno 12mm, carico dinamico 960N, statico 6720N, dimensioni 39 x 43 x 35mm |  |  |  | 617-4696 | RS COMPONENTS | 2 | €56.49 | €112.98 | 137.84
19 | Giunto in alluminio 5 mm – 8 mm |  |  |  | 8300-HUB5MM8 | FUTURA ELETTRONICA (FUTURA GROUP) | 3 | €1.48 | €4.44
20 | Interruttore DIP NDS-03-V, SPST, 25 mA, 3 posizioni, attuatore a Rialzato, Foro passante |  |  |  | NDS-03-V | RS COMPONENTS | 1 | €5.80 | €5.80 | È 1 sacchetto da 5 componenti
21 | Copertura protettiva ebm-papst in Plastica, 80 x 80mm, ventola da 80mm |  |  |  | 92162-2-2929 | RS COMPONENTS | 2 | €3.80 | €7.60 | 9.27
22 | Raspberry Pi 5 versione con 16 GB di memoria |  |  |  | 7310-RPI5-16GB | FUTURA ELETTRONICA (FUTURA GROUP) | 1 | €144.30 | €144.30
23 | Servo motore 10.5kg/cm ingranaggi metallo 180° |  |  |  | 8300-MG946R | FUTURA ELETTRONICA (FUTURA GROUP) | 1 | €6.63 | €6.63
24 | Intenso High Performance Scheda microSDHC 8 GB Class 10 incl. Adattatore S |  |  |  | 3413460 | CONRAD | 1 | €3.50 | €3.50
25 | Kingston Canvas Select Plus Scheda microSDXC 128 GB Class 10 UHS-I |  |  |  | SDCS2/128GBSP | CONRAD | 1 | €8.57 | €8.57
26 | SanDisk microSDXC Ultra 64GB (A1/UHS-I/Cl.10/140MB/s) + Adapter "Mobile" Scheda microSDXC 64 GB A1 Application Performan |  |  |  | SDSQUAB-064G-GN6MA | CONRAD | 1 | €7.01 | €7.01
27 | Angolare 90° in alluminio pressofuso |  |  |  | 7350-ANG90ALLU | FUTURA ELETTRONICA (FUTURA GROUP) | 30 | €0.50 | €15.00
28 | Cramolin GRAPHIT 1281411 Lacca 200 ml |  |  |  | 820571-62 | CONRAD | 1 | €22.99 | €22.99
29 | Filamento per stampante 3D NANOVIA, PET-G, Nero, diam. 1.75mm |  |  |  | 635-147 | RS COMPONENTS | 2 | €21.75 | €43.50 | 53.07
30 | 10 dischi magnetici 8x3 mm |  |  |  | 8220-MAGNET5 | FUTURA ELETTRONICA (FUTURA GROUP) | 2 | €6.00 | €12.00
31 | Diodo DiodesZetex, Foro passante, 10 A, 100 V, TO-220, Bassa dispersione, 3 Pin |  |  |  | SDT10A100CT | RS COMPONENTS | 1 | €2.92 | €2.92 | è una confezione da 10, quindi solo 1 confezione
32 | Contatto a crimpare JST PH Totale poli 1 BPH-002T-P0.5S 1 pz. |  |  |  | BPH-002T-P0.5S | CONRAD | 50 | €0.05 | €2.34 | l’ordine minimo è di 50, quindi è l’ordine minimo
33 | Connettore maschio da incasso (standard) JST PH Totale poli 8 Passo: 2 mm S8B-PH-SM4-TB (LF)(SN) 1 pz. |  |  |  | S8B-PH-SM4-TB (LF)(SN) | CONRAD | 5 | €1.01 | €5.03 | è una confezione da 5, quindi solo 1 confezione
34 | Connettore maschio da incasso (standard) JST PH Totale poli 4 Passo: 2 mm S4B-PH-SM4-TB (LF)(SN) 1 pz. |  |  |  | S4B-PH-SM4-TB (LF)(SN) | CONRAD | 7 | €0.28 | €1.96 | è una confezione da 7, quindi solo 1 confezione
35 | Connettore maschio da incasso (standard) JST PH Totale poli 3 Passo: 2 mm S3B-PH-SM4-TB (LF)(SN) 1 pz. |  |  |  | S3B-PH-SM4-TB (LF)(SN) | CONRAD | 7 | €0.44 | €3.11 | è una confezione da 7, quindi solo 1 confezione
36 | Connettore maschio da incasso (standard) JST PH Totale poli 2 Passo: 2 mm S2B-PH-SM4-TB (LF)(SN) 1 pz. |  |  |  | S2B-PH-SM4-TB (LF)(SN) | CONRAD | 10 | €0.40 | €4.00 | è una confezione da 10, quindi solo 1 confezione
37 | Fischer Elektronik Connettore maschio (standard) Numero di righe: 1 Poli per fila: 20 SL LP 5 SMD 051/ 20/S 1 pz. |  |  |  | SL LP 5 SMD 051/ 20/S | CONRAD | 10 | €0.63 | €6.32
38 | Portabatterie 9V PP3, montaggio PCB, contatti Montaggio su circuito stampato |  |  |  | 185-4728 | RS COMPONENTS | 1 | €2.09 | €2.09
39 | Batteria 9V RS PRO, 1.2Ah, Litio diossido di manganese |  |  |  | 784-5992 | RS COMPONENTS | 1 | €12.21 | €12.21
40 | Condensatore RS PRO, 4700μF, 35V cc, ±20%, 105°C, Radiale, Foro passante |  |  |  | 711-1374 | RS COMPONENTS | 2 | €1.04 | €2.08 | è una confezione da 2, quindi solo 1 confezione
41 | Condensatore RS PRO, 470μF, 35V cc, ±20%, 105°C, Radiale, Foro passante |  |  |  | 711-1299 | RS COMPONENTS | 10 | €0.42 | €4.17 | è una confezione da 10, quindi solo 1 confezione
42 | Potenziometro trimmer Bourns, 5kΩ, 12 giri, Regolazione dall'alto, Su foro |  |  |  | 769-2243 | RS COMPONENTS | 4 | €1.88 | €7.52
43 | Adattatore AC/DC RS PRO 24V cc, 3A, spina IEC 320 C14 |  |  |  | 204-7566 | RS COMPONENTS | 1 | €30.37 | €30.37
44 | Presa DC da pannello 5,5 x 2,1 mm |  |  |  | 1606-DCPLUG | FUTURA ELETTRONICA (FUTURA GROUP) | 4 | €0.78 | €3.12
45 | Case per Raspberry Pi Raspberry Pi ABS serie Pi Case, per Raspberry Pi 5 Nero |  |  |  | 219-256 | RS COMPONENTS | 1 | €9.34 | €9.34
46 | Alimentatore per Raspberry Pi Raspberry Pi, presa USB di tipo C con Connettore maschio EU, cavo da 1.2m |  |  |  | 219-261 | RS COMPONENTS | 1 | €11.68 | €11.68
47 | Morsettiera per cavo JST PHR Totale poli 8 Passo: 2 mm PHR-8 1 pz. |  |  |  | PHR-8 | CONRAD | 15 | €0.10 | €1.50 | 15 è il numero minimo di pezzi ordinabile
48 | Morsettiera per cavo JST PHR Totale poli 4 Passo: 2 mm PHR-4 1 pz. |  |  |  | PHR-4 | CONRAD | 30 | €0.11 | €3.30 | 30 è il numero minimo di pezzi ordinabile
49 | Morsettiera per cavo JST PHR Totale poli 3 Passo: 2 mm PHR-3 1 pz. |  |  |  | PHR-3 | CONRAD | 30 | €0.09 | €2.70 | 30 è il numero minimo di pezzi ordinabile
50 | Morsettiera per cavo JST PHR Totale poli 2 Passo: 2 mm PHR-2 1 pz. |  |  |  | PHR-2 | CONRAD | 30 | €0.07 | €2.10 | 30 è il numero minimo di pezzi ordinabile | Totale
51 | 3M 3302/20 100 SF Cavo piatto Passo: 1.27 mm 20 x 0.08 mm² Colorato Merce a metro |  |  |  | 3302/20 100 SF | CONRAD | 1 | €3.93 | €3.93 | 1 unità equivale a 1 metro | 847.65 €
 |  |  | schei totali
 |  |  | 1086.736154
 |  | 113.2638462 |  |  |  | 17.30769231
 |  |  |  |  |  | 61.53846154
 |  |  |  |  |  | 24.35897436
 |  |  |  |  |  | 6.41025641
 |  |  |  |  |  | 17.94871795
 |  | 847.65 € |  |  |  | 24.35897436
 |  |  |  |  |  | 41.02564102
 |  | 1086- |  |  |  | 3.205128205
 |  |  |  |  |  | 4.487179487
 |  |  |  |  |  | 16.06410256
 |  |  |  |  |  | 7.166666666
 |  |  |  |  |  | 15.38461538
 |  |  |  |  |  | 23.07692308
 |  |  |  |  |  | 30.76923077
 |  |  |  |  |  | 11.53846154
 |  |  |  |  |  | 87.94871795
 |  |  |  |  |  | 32.46153846
 |  |  |  |  |  | 144.8461538
 |  |  |  |  |  | 5.692307692
 |  |  |  |  |  | 7.435897436
 |  |  |  |  |  | 9.743589743
 |  |  |  |  |  | 185
 |  |  |  |  |  | 8.5
 |  |  |  |  |  | 4.487179487
 |  |  |  |  |  | 10.98717949
 |  |  |  |  |  | 8.987179487
 |  |  |  |  |  | 19.23076923
 |  |  |  |  |  | 29.47435897
 |  |  |  |  |  | 55.76923077
 |  |  |  |  |  | 15.38461538
 |  |  |  |  |  | 3.743589743
 |  |  |  |  |  | 3
 |  |  |  |  |  | 6.448717948
 |  |  |  |  |  | 2.512820513
 |  |  |  |  |  | 3.99
 |  |  |  |  |  | 5.128205128
 |  |  |  |  |  | 8.102564102
 |  |  |  |  |  | 2.679487179
 |  |  |  |  |  | 15.65384615
 |  |  |  |  |  | 2.669230769
 |  |  |  |  |  | 5.346153846
 |  |  |  |  |  | 9.641025641
 |  |  |  |  |  | 38.93589743
 |  |  |  |  |  | 4
 |  |  |  |  |  | 11.97435897
 |  |  |  |  |  | 14.97435897
 |  |  |  |  |  | 1.923076923
 |  |  |  |  |  | 4.230769231
 |  |  |  |  |  | 3.461538461
 |  |  |  |  |  | 2.692307692
 |  |  |  |  |  | 5.038461538
 |  |  |  |  |  | 0
 |  |  |  |  |  | 0
 |  |  |  |  |  | 0
 |  |  |  |  |  | 0
 |  |  |  |  |  | 0
 |  |  |  |  |  | 0
 |  |  |  |  |  | 0
 |  |  |  |  |  | 0
 |  |  |  |  |  | 0
 |  |  |  |  |  | 0
 |  |  |  |  |  | 0
 |  |  |  |  |  | 0
 |  |  |  |  |  | 0
 |  |  |  |  |  | 0
 |  |  |  |  |  | 0
 |  |  |  |  |  | 0
 |  |  |  |  |  | 0
 |  |  |  |  |  | 0
 |  |  |  |  |  | 0
 |  |  |  |  |  | 0
 |  |  |  |  |  | 0
 |  |  |  |  |  | 0
 |  |  |  |  |  | 0
 |  |  |  |  |  | 0
 |  |  |  |  |  | 0
 |  |  |  |  |  | 0
 |  |  |  |  |  | 0
 |  |  |  |  |  | 0
 |  |  |  |  |  | 0
 |  |  |  |  |  | 0
 |  |  |  |  |  | 0
 |  |  |  |  |  | 0
 |  |  |  |  |  | 0
 |  |  |  |  |  | 0
 |  |  |  |  |  | 0
 |  |  |  |  |  | 0
 |  |  |  |  |  | 0
 |  |  |  |  |  | 0
 |  |  |  |  |  | 0
 |  |  |  |  |  | 0
 |  |  |  |  |  | 0
 |  |  |  |  |  | 0
 |  |  |  |  |  | 0
 |  |  |  |  |  | 0
 |  |  |  |  |  | 0
 |  |  |  |  |  | 0
 |  |  |  |  |  | 0
 |  |  |  |  |  | 0
 |  |  |  |  |  | 0
 |  |  |  |  |  | 0
 |  |  |  |  |  | 0
 |  |  |  |  |  | 0
 |  |  |  |  |  | 0
 |  |  |  |  |  | 0
 |  |  |  |  |  | 0
 |  |  |  |  |  | 0
 |  |  |  |  |  | 0
 |  |  |  |  |  | 0
 |  |  |  |  |  | 0
 |  |  |  |  |  | 0
 |  |  |  |  |  | 0
 |  |  |  |  |  | 0
 |  |  |  |  |  | 0
 |  |  |  |  |  | 0
 |  |  |  |  |  | 0
 |  |  |  |  |  | 0
 |  |  |  |  |  | 0
 |  |  |  |  |  | 0
 |  |  |  |  |  | 0
 |  |  |  |  |  | 0
 |  |  |  |  |  | 0
 |  |  |  |  |  | 0
 |  |  |  |  |  | 0
 |  |  |  |  |  | 0
 |  |  |  |  |  | 0
 |  |  |  |  |  | 0
 |  |  |  |  |  | 0
 |  |  |  |  |  | 0
 |  |  |  |  |  | 0
 |  |  |  |  |  | 0
 |  |  |  |  |  | 0
 |  |  |  |  |  | 0
 |  |  |  |  |  | 0
 |  |  |  |  |  | 0
 |  |  |  |  |  | 0
 |  |  |  |  |  | 0
 |  |  |  |  |  | 0
 |  |  |  |  |  | 0
 |  |  |  |  |  | 0

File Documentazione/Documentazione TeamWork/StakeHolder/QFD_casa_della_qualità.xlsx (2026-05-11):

 | QFD: House of Quality
Sede: | ITS Meccatronico Montebelluna - Castelfranco Veneto
Gruppo: | Team 1
Data: | 2025-02-04
Correlazione
Positiva |  | +
Negativa |  | −
Nessuna Correlazione
Relazione |  |  |  |  |  |  |  |  |  |  |  |  |  |  |  | ~~+~~
Forte |  | ●
Media |  | ○ |  |  |  |  |  |  |  |  |  |  |  |  |  | +
Debole |  | ▽ |  |  |  |  |  |  |  |  |  |  |  |  |  |  |  |  |  |  | +
 |  |  |  |  |  |  |  |  |  |  |  |  |  | +
 |  |  |  |  |  |  |  |  |  |  |  |  | + |  |  |  |  | − |  |  | − |  | +
 |  |  |  |  |  |  |  |  |  |  | + |  |  |  |  | +
 |  |  |  |  |  |  | + |  |  | + |  |  |  |  |  |  |  |  |  |  | + |  | −
 |  |  |  |  |  |  |  | + |  |  | + |  |  |  |  |  |  |  | + |  |  |  |  |  | +
 |  |  | Colonna # |  | 1 | 2 |  |  | 3 |  |  | 4 |  |  | 5 |  | 6 |  |  | 7 |  | 8 |  | 9 |  | 10 | 11 | 12 | 13 | 14
 | Riga # | Importanza per il cliente (da 1 a 10) |  | Caratteristiche funzionali | Suddivisione discreta delle cialde | Di facile manutenzione |  |  | Tecnologico |  |  | Sicuro |  |  | serbatoio capiente |  | Materiale 3D PLA per prototipazione |  |  | Peso del macchinario |  | Costo di produzione |  | Dimensioni ridotte |  | Vibrazioni attutite
 |  |  | Richieste del cliente/utilizzatore (Esplicite e implicite)
 | 1 | 8 | Silenzioso |  | ▽ |  |  |  | ○ |  |  |  |  |  |  |  |  |  |  | ○ |  |  |  | ○ |  | ●
 | 2 | 8 | Compatto |  | ● | ● |  |  | ○ |  |  |  |  |  | ○ |  |  |  |  | ○ |  |  |  | ●
 | 3 | 9 | Discretamente Sicuro |  |  | ○ |  |  | ○ |  |  | ●
 | 4 | 7 | Manutenzione Bassa e agevolata |  | ▽ | ● |  |  | ● |  |  | ○ |  |  | ▽ |  | ● |  |  | ○ |  |  |  | ○
 | 5 | 7 | Basso costo di mantenimento |  | ▽ | ○ |  |  | ○ |  |  |  |  |  |  |  | ●
 | 6 | 8 | Prezzo economico |  |  | ▽ |  |  |  |  |  |  |  |  | ○ |  | ● |  |  |  |  | ●
 | 7 | 10 | Facilità di utilizzo |  | ○ | ▽ |  |  | ○ |  |  | ● |  |  | ○ |  |  |  |  |  |  |  |  | ▽
 | 8 | 9 | Suddivisione efficace delle cialde |  | ● |  |  |  | ○
 | 9 | 8 | Serbatoio capiente |  | ○ | ○ |  |  | ▽ |  |  |  |  |  | ●
 | 10 | 7 | Facilità di installazione |  |  |  |  |  | ○ |  |  | ▽ |  |  |  |  |  |  |  | ● |  |  |  | ● |  | ●
 | 11
 | 12
 | 13
 | 14
 | 15
 | 16
 |  |  | Target |  | sudivisione tramite processo automatizzato | realizzata con parti meccaniche e scheda elettonica facilmente reperibile |  |  | realizzato tramite scheda elettronica orientata alla connettività IoT |  |  | realizzato tramite l'impiego di sensori per evitare infortuni |  |  | serbatoio contenimento cialde di 1,5l e serbatoio fondi di caffè di 0,70l |  | Materiale 3D ti tipo plastico e compostabile, utile per la prototipazione e manutenzione |  |  | Peso del macchinario ridotto per facilitare l'ultilizzo, la manutenzione e l'installazione |  | Costo di produzione relativamente basso |  | Dimensioni ridotte per facilitare l'ultilizzo, la manutenzione e l'installazione |  | Vibrazioni attutite per ridurre oscillazioni sulla base di appoggio e per garantire una minore usura dei componenti
 |  |  | Decapsulator |  | 4.5 | 4.5 |  |  | 4 |  |  | 4.5 |  |  | 3 |  | 3 |  |  | 4.5 |  | 4.5 |  | 4.5 |  | 3.75
 |  |  | White Star : Twister |  | 5 | 2 |  |  | 4 |  |  | 4.75 |  |  | 5 |  | 0 |  |  | 1.5 |  | 1 |  | 1 |  | 2
 |  |  | Competitor #2: nome prodotto
 |  |  | Competitor #3: nome prodotto
 |  |  | Colonna # |  | 1 | 2 |  |  | 3 |  |  | 4 |  |  | 5 |  | 6 |  |  | 7 |  | 8 |  | 9 |  | 10 | 11 | 12 | 13 | 14
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

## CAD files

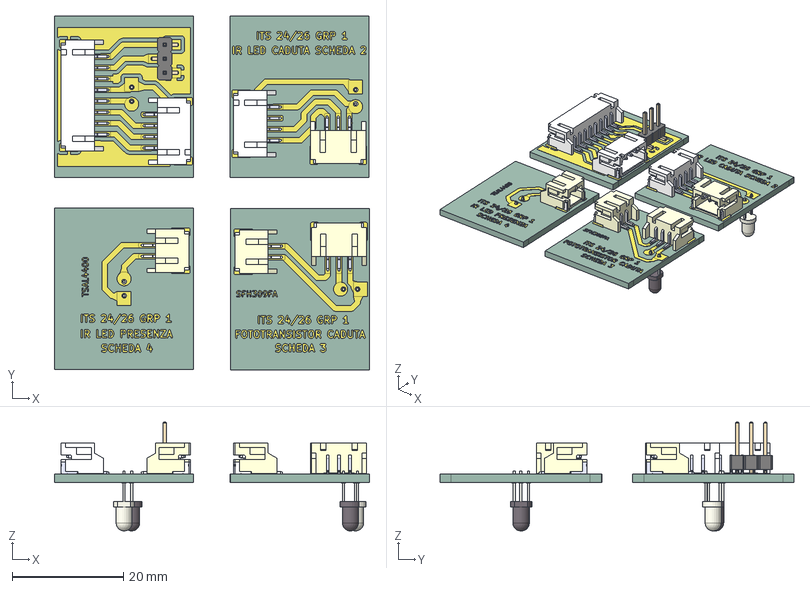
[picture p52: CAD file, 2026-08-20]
Hardware/Rx_Tx_Scivolo_Decapsulator/Rx_Tx_Scivolo_Decapsulator.step
56.7 x 63.6 x 19.6 mm
SxB-PH-SM4-TB white_8
LED_D3.0mm_Clear x 2
S2B-PH-SM4-TB x 2
LED_D3.0mm_IRBlack x 2
PinHeader_1x03_P2.54mm_Vertical_SMD_Pin1Right
S3B-PH-SM4-TB (LF)(SN)--3DModel-STEP-269445 x 2
SxB-PH-SM4-TB white_4 x 2
Rx_Tx_Scivolo_Decapsulator_copper
Rx_Tx_Scivolo_Decapsulator_PCB_1
Rx_Tx_Scivolo_Decapsulator_PCB_2
Rx_Tx_Scivolo_Decapsulator_PCB_3
Rx_Tx_Scivolo_Decapsulator_PCB_4

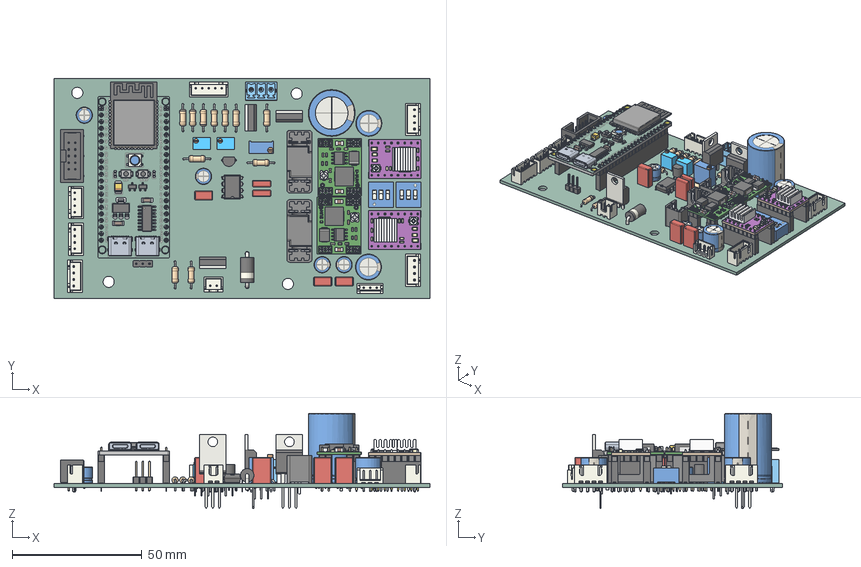
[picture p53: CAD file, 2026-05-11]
Hardware/SCHEDA_PRINCIPALE/STEP_Blender/KDT_Hierarchical_KiBot.step
145.0 x 85.0 x 36.8 mm
R_Axial_DIN0207_L6.3mm_D2.5mm_P10.16mm_Horizontal x 11
Potentiometer_Bourns_3266W_Vertical x 2
D_DO-201AD_P12.70mm_Horizontal
JST_XH_B4B-XH-A_1x04_P2.50mm_Vertical x 5
Driver DRV8825 x 2
PBS-8 x 4
TO-220-3_Vertical x 3
CP_Radial_D6.3mm_P2.50mm x 4
JST_XH_B5B-XH-A_1x05_P2.50mm_Vertical
main001 x 2
silk-TOP x 2
pins x 2
silk-bot x 2
comp-top x 2
PinSocket_1x02_P2.54mm_Vertical x 8
PinHeader_1x02_P2.54mm_Vertical x 8
CP_Radial_D18.0mm_P7.50mm
JST_EH_B3B-EH-A_1x03_P2.50mm_Vertical
LED_0603_1608Metric x 2
LED_WS2812B_PLCC4_5.0x5.0mm_P3.2mm
PinHeader_1x21_P2.54mm_Vertical x 2
ESP32-S3-WROOM-2
SOIC-16_3.9x9.9mm_P1.27mm
SOT-23 x 2
SOT-223
SW_SPST_TS-1088-xR025 x 2
C_1206_3216Metric x 2
CP_EIA-3528-21_Kemet-B
ESP32-S3-N16R8_GOOUUU_TECH_copper
ESP32-S3-N16R8_GOOUUU_TECH_pad
ESP32-S3-N16R8_GOOUUU_TECH_via
ESP32-S3-N16R8_GOOUUU_TECH_silkscreen
ESP32-S3-N16R8_GOOUUU_TECH_soldermask x 2
ESP32-S3-N16R8_GOOUUU_TECH_PCB
PinSocket_1x21_P2.54mm_Vertical x 2
SW_DIP_SPSTx03_Slide_9.78x9.8mm_W7.62mm_P2.54mm x 2
JST_XH_B2B-XH-A_1x02_P2.50mm_Vertical
DIP-8_W7.62mm
PinHeader_1x03_P2.54mm_Vertical
TBP02R2-381-03BE--3DModel-STEP-242080
IDC-Header_2x05_P2.54mm_Vertical
CP_Radial_D10.0mm_P5.00mm x 2
C_Rect_L7.0mm_W3.5mm_P5.00mm x 3
C_Rect_L7.0mm_W2.5mm_P5.00mm x 2
Potentiometer_Bourns_3296W_Vertical
TO-92_Inline_Wide
Scheda_principale_PCB

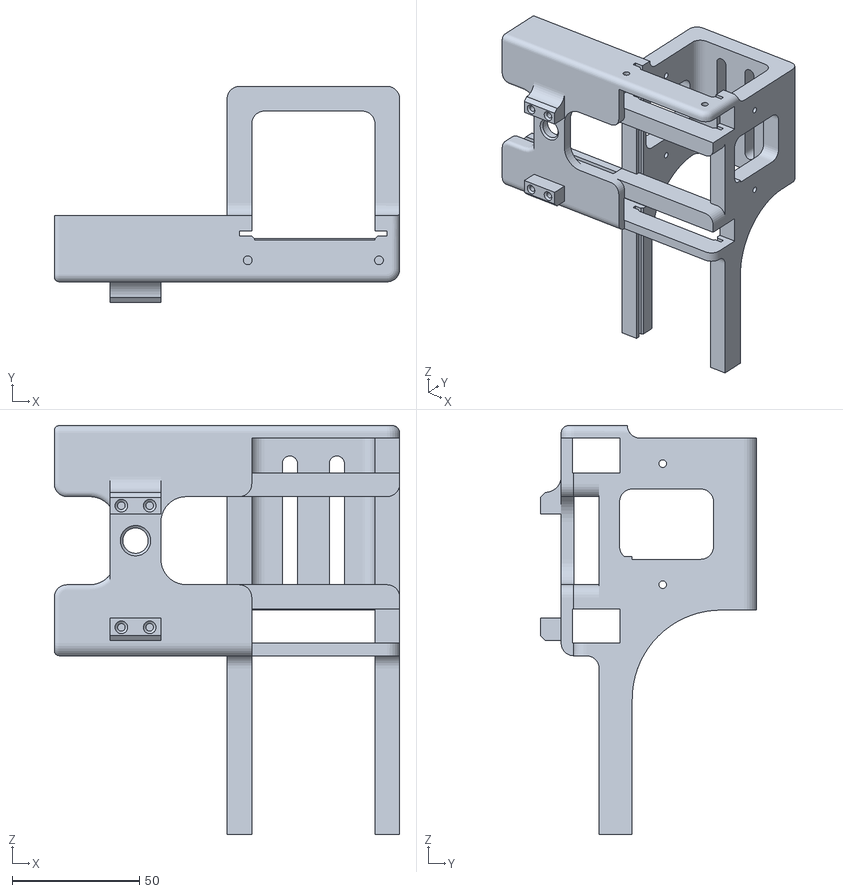
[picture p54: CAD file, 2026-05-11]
Meccanica/magazzino_cialde/magazzino_cialde_decapsulator.stl
136.0 x 85.2 x 161.0

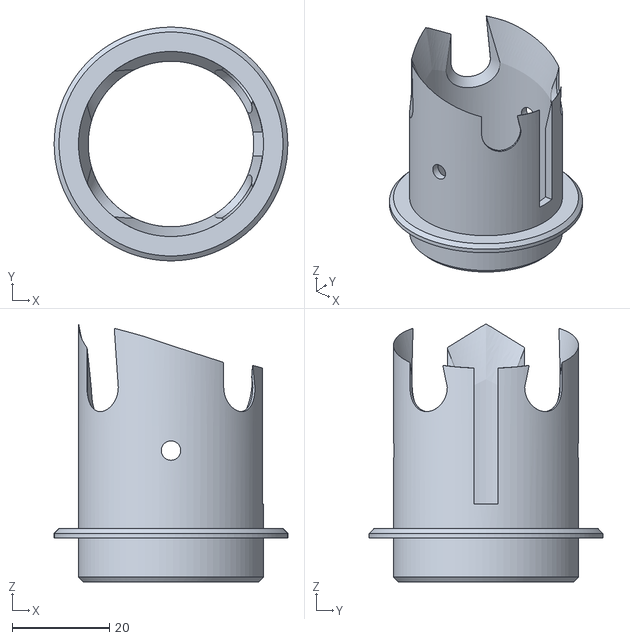
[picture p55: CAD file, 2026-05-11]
Meccanica/punzoni/punzone .stl
48.0 x 48.0 x 53.0

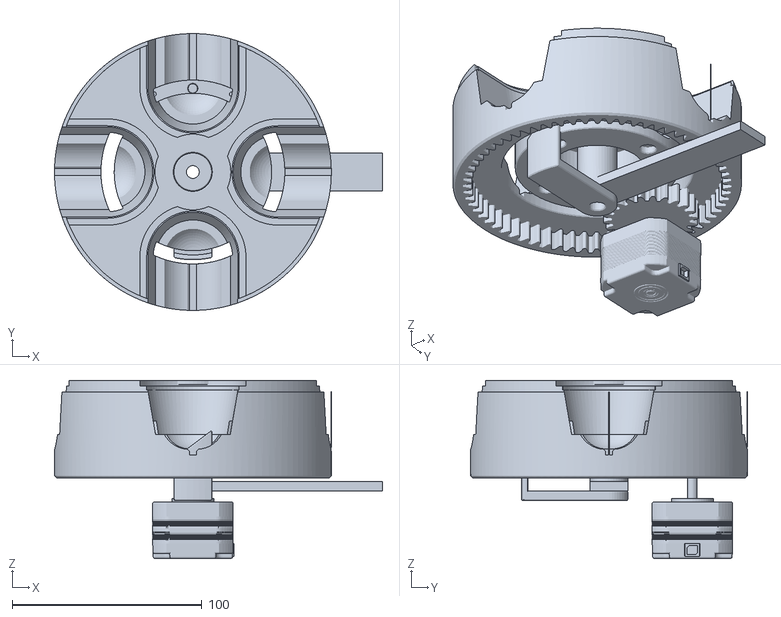
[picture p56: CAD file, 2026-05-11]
Meccanica/ralla 4 posizioni/ralla_4_posizioni v1.stl
173.0 x 146.0 x 93.9

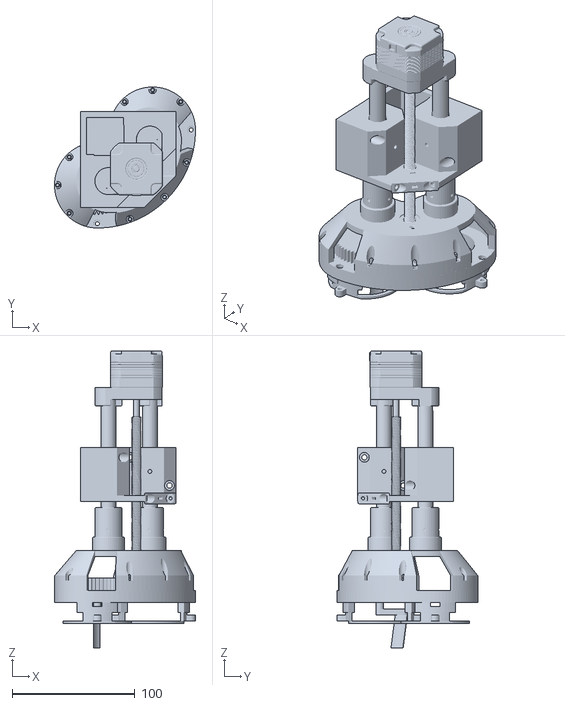
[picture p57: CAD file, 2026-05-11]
Meccanica/Sistema di punzonatura && raschiatura/sistema_punzonatura-raschiatutra v1.stl
115.0 x 115.0 x 242.2

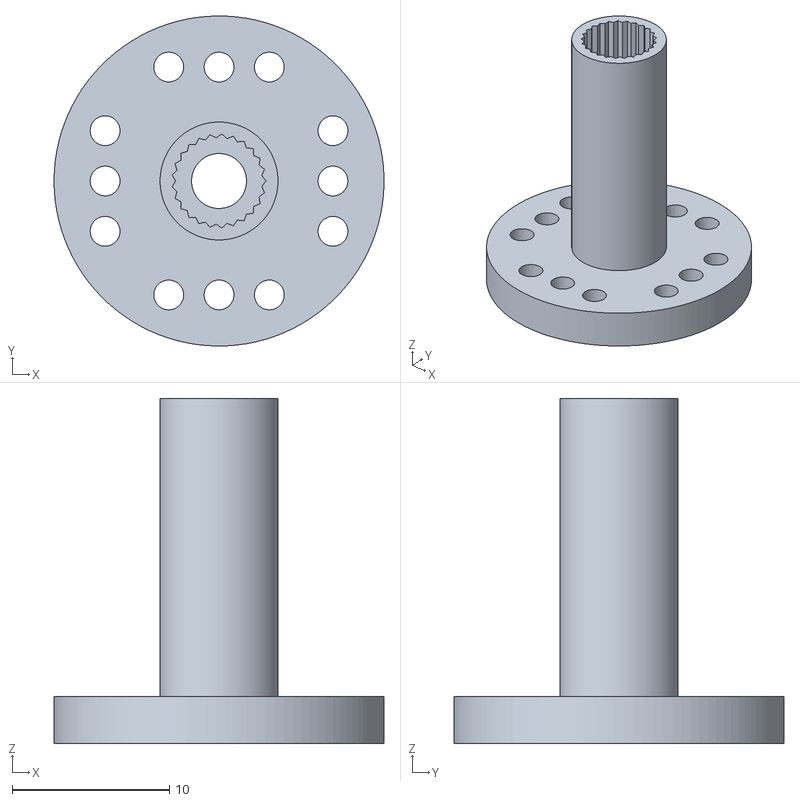
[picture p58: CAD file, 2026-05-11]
Meccanica/magazzino_cialde/ServoMotor_flangia_.stl
21.0 x 21.0 x 22.0

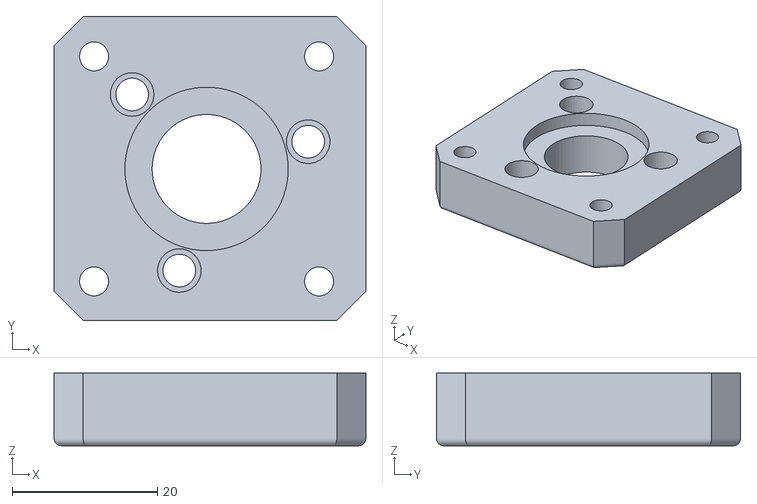
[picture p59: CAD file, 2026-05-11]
Meccanica/Sistema di punzonatura && raschiatura/supporto_superiore_motore_fasiol.stl
42.9 x 41.9 x 10.0

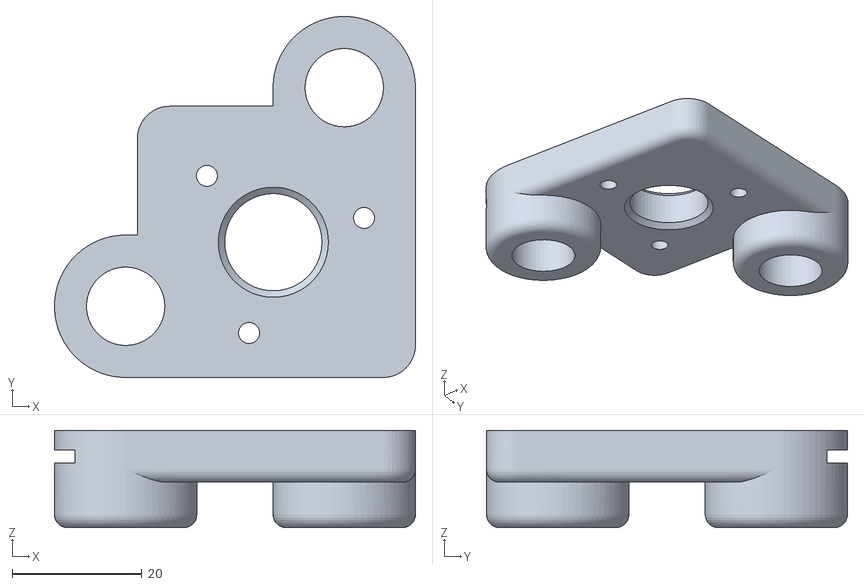
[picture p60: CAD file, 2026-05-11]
Meccanica/Sistema di punzonatura && raschiatura/Supporto_sottostanate_motore_fasiol.stl
55.7 x 55.7 x 15.0

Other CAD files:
Hardware/Rx_Tx_Scivolo_Decapsulator/Rx_Tx_Scivolo_Decapsulator.stl

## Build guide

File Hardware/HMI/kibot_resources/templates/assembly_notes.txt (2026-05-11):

ASSEMBLY NOTES (UNLESS OTHERWISE SPECIFIED)

1)	DO NOT POPULATE PARTS ARE MARKED WITH A RED CROSS.

2)	DO NOT POPULATE PARTS ARE NOT PRESENT IN THE BOM.

3)	IF CONFLICTING INFORMATION IS FOUND BETWEEN THE ASSEMBLY
	FILE AND BOM, BOM SHOULD BE USED AS THE MAIN SOURCE.

4)	CONFORMAL COATING IS NOT REQUIRED.

5)	DOT IDENTIFIES PIN #1 LOCATION AND DEVICE ORIENTATION
	WHEN VIEWED FROM THE TOP.

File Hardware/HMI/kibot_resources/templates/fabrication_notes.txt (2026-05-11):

FABRICATION NOTES (UNLESS OTHERWISE SPECIFIED)

1)	FABRICATE PER IPC-6012A CLASS 2.

2)	OUTLINE DEFINED IN SEPARATE GERBER FILE WITH
	"Edge_Cuts.GBR" SUFFIX.

	DIMENSIONS OF CIRCUMSIZED RECTANGLE SHOWN ON THIS
	DRAWING FOR REFERENCE ONLY.

3)	SEE SEPARATE DRILL FILES WITH ".DRL" SUFFIX 
	FOR HOLE LOCATIONS.

	SELECTED HOLE LOCATIONS SHOWN ON THIS DRAWING 
	FOR REFERENCE ONLY.

4)	SURFACE FINISH: ${pcb_finish_cap}

5)	SOLDERMASK ON BOTH SIDES OF THE BOARD SHALL 
	BE LPI, COLOR ${solder_mask_color_text_cap}.

6)	SILK SCREEN LEGEND TO BE APPLIED PER LAYER 
	STACKUP USING ${silk_screen_color_text_cap} NON-CONDUCTIVE EPOXY INK.

7)	ALL VIAS ARE TENTED ON BOTH SIDES UNLESS 
	SOLDERMASK OPENED IN GERBER.

8)	VENDOR SHOULD FOLLOW ROHS COMPLIANT PROCESS 
	AND Pb FREE FOR MANUFACTURING

9)	PCB MATERIAL REQUIREMENTS:

	A.	FLAMMABILITY RATING MUST MEET OR EXCEED 
		UL94V-0 REQUIREMENTS.
	B.	Tg 170 C OR EQUIVALENT.
	C.	EQUIVALENT MATERIAL SHALL BE RoHS COMPLIANT, 
		HALOGEN FREE AND APPROVED BY ${COMPANY_cap}.

10)	DESIGN GEOMETRY MINIMUM FEATURE SIZES:

	BOARD SIZE				${bb_w_mm} × ${bb_h_mm} mm
	BOARD THICKNESS		${thickness_mm} mm
	TRACE WIDTH			${track_mm} mm
	TRACE TO TRACE		${clearance_mm} mm
	MIN. HOLE (PTH)			${drill_pth_real_mm} mm
	MIN. HOLE (NPTH)		${drill_npth_real_mm} mm
	ANNULAR RING			${oar_mm} mm
	COPPER TO HOLE		${c2h_mm} mm
	COPPER TO EDGE		${c2e_mm} mm
	HOLE TO HOLE			${h2h_mm} mm
#?stackup and impedance_controlled

#?stackup and impedance_controlled
11)	REFER TO IMPEDANCE TABLE FOR IMPEDANCE CONTROL REQUIREMENTS.
#?stackup and impedance_controlled

#?stackup and impedance_controlled
12)	CONFIRM SPACE WIDTHS AND SPACINGS.

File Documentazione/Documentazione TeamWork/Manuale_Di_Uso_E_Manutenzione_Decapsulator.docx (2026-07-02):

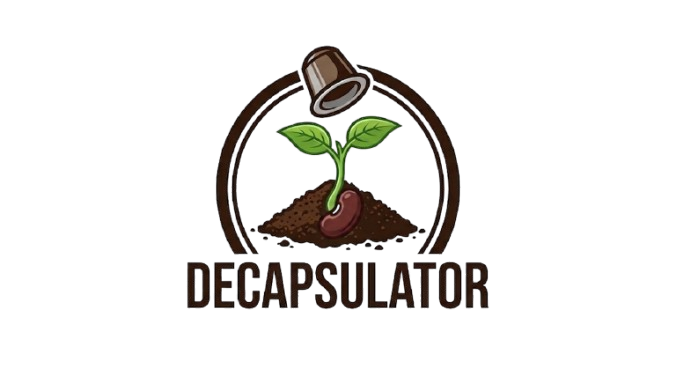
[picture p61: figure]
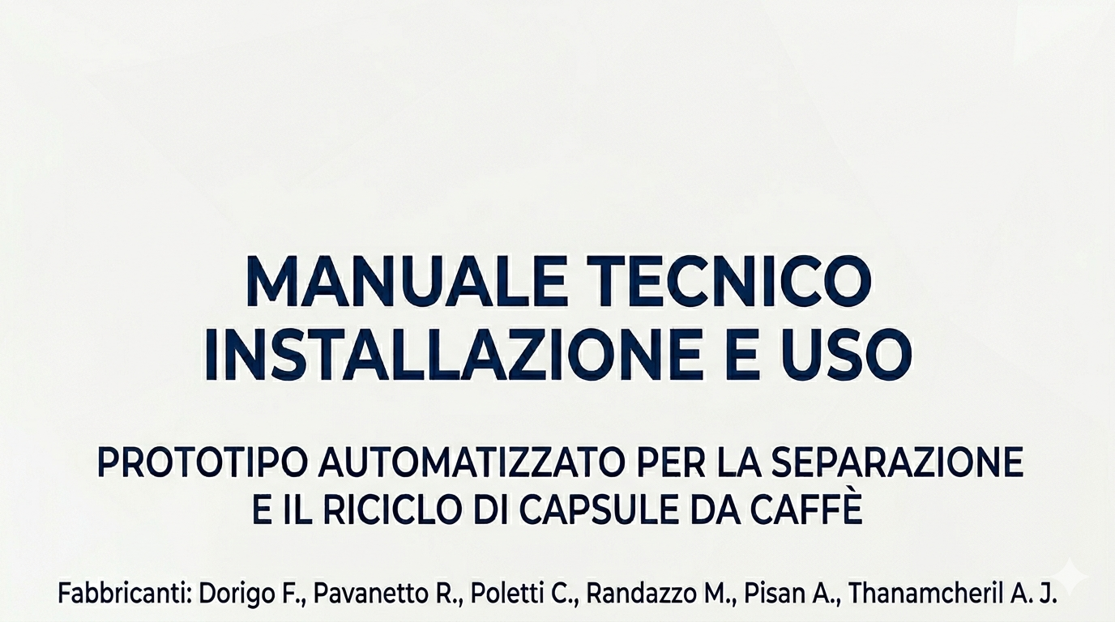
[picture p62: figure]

Indice - IT

Sommario - IT

1. DICHIARAZIONE CE DI CONFORMITÀ 5

1.1 Dati di targa 6

2. IDENTIFICAZIONE DELLA MACCHINA 7

2.1 Disegno Prototipo 7

2.2 Descrizione Generale: 8

2.3 Destinazione d'uso: 9

2.4 INFORMAZIONE SULLA SICUREZZA 9

2.5 Rischi Residui 10

2.6 Tabella dei rischi 14

3. TRASPORTO E DIMENSIONI 15

4. REGOLE GENERALI PER L’USO DELLA MACCHINA 15

4.1 Istruzioni d’uso 16

5. INSTALLAZIONE MACCHINA 16

5.1 Installazione dell’apparecchio 16

5.2 Cablaggi principali: 17

6 Pulizia dell’apparecchio 17

7 Gestione delle Criticità e Guasti 17

7.1 In caso di guasto dell’apparecchio 17

7.2 Uso improprio dell’apparecchio 18

8. ALIMENTAZIONE ELETTRICA 18

8.1Istruzioni per il cavo di alimentazione 18

9. SICUREZZA E MANUTENZIONE 19

9.1 Dispositivi di Protezione Individuale (DPI) 19

9.2 Precauzioni di Sicurezza 20

9.3 Manutenzione Periodica 20

9.4 Manutenzione mirata tramite pagina di diagnostica sull’interfaccia utente 20

10. GESTIONE DELLE EMERGENZE 22

11. REGISTRO DELLE MANUTENZIONI 22

12. SMALTIMENTO 23

12.1 Procedura di Smantellamento 23

12.2 Riciclaggio dei Materiali 23

Summary - EN

1. EC declaration of conformity 26

1.1 Plate data 27

2. Machine identification 28

2.1 Prototype Design 28

2.2 General Description: 29

2.3 Intended use: 30

2.4 Information on the security 30

2.5 Residual risks 31

2.6 Risk Table 35

3. TRANSPORT AND DIMENSIONS 36

4. GENERAL RULES FOR THE USE OF THE MACHINE 36

4.1 Instructions for use 37

5. MACHINE INSTALLATION 37

5.1 Installation of the appliance 37

5.2 Main wiring: 38

6 Cleaning the appliance 38

7 Criticality and Fault Management 38

7.1 In the event of failure of the appliance 38

7.2 Improper use of the appliance 39

8. POWER SUPPLY 39

8.1 Instructions for the power cord 39

9. SAFETY AND MAINTENANCE 40

9.1 Personal Protective Equipment (PPE) 40

9.2 Safety Precautions 41

9.3 Periodic Maintenance 41

9.4 Targeted maintenance via diagnostics page on the user interface 41

10. EMERGENCY MANAGEMENT 43

11. MAINTENANCE LOG 43

12. DISPOSAL 44

12.1 Dismantling procedure 44

12.2 Recycling of materials 44

Sede:

Via Sansovino, 6, 31044 Montebelluna TV

Via Avenale, 6, 31033 Castelfranco Veneto TV

"La presente documentazione tecnica è stata concepita per guidare l'operatore nell'interazione con il prototipo DECAPSULATOR, un sistema nato da un approfondito sviluppo didattico focalizzato sulla precisione costruttiva e l’efficienza funzionale. Le direttive qui riportate sono fondamentali per esplorare le potenzialità del dispositivo, assicurando al contempo il mantenimento dei massimi standard di sicurezza operativa. Data la natura sperimentale e accademica del progetto, è tassativo operare sotto costante supervisione e attenersi scrupolosamente alle procedure illustrate, poiché il team di sviluppo declina ogni responsabilità per utilizzi impropri o difformi da quanto prescritto. La corretta conduzione del sistema rappresenta per noi la validazione finale del percorso intrapreso durante l’anno scolastico."

# 1. DICHIARAZIONE CE DI CONFORMITÀ

Dichiarazione CE in lingua originale.

Il presente manuale è parte integrante del prodotto e deve essere conservato per tutta la durata di vita dello stesso.

Il presente prototipo è stato progettato seguendo i criteri di sicurezza delle varie direttive:

- Direttiva Macchine 2006/42/CE: Applicabile in quanto l'apparecchio presenta organi in movimento, tra cui tamburo rotante, paratia di selezionatura servo-attivata e punzone, i quali comportano rischi meccanici.
- Direttiva Bassa Tensione (LVD) 2014/35/UE: Consultata per la sicurezza dei componenti elettrici e dei circuiti di alimentazione.
- Direttiva Compatibilità Elettromagnetica (EMC) 2014/30/UE: Applicabile per garantire che l’elettronica non interferisca con altre apparecchiature circostanti al macchinario.
- Direttiva RoHS 2011/65/UE: Consultata per garantire l'assenza di sostanze pericolose nei componenti elettronici e nei materiali di apporto.

Queste norme sono state utilizzate per i calcoli, i dimensionamenti meccanici e la definizione dei disegni 2D/3D:

- UNI EN ISO 12100:2010: Sicurezza del macchinario - Principi generali di progettazione - Valutazione e attenuazione del rischio.
- UNI EN ISO 13857:2020: Distanze di sicurezza per impedire il raggiungimento di zone pericolose con gli arti superiori (utilizzata per dimensionare l'imbocco delle capsule e i carter del tamburo).
- UNI EN ISO 14119:2013: Dispositivi di interblocco associati ai ripari (utilizzata per la scelta e l'installazione del micro-switch di sicurezza sul coperchio).
- CEI EN 60204-1: Sicurezza dell'equipaggiamento elettrico delle macchine (utilizzata per lo schema elettrico e funzionale).

NOTA: Destinazione d'uso: prototipo a scopo didattico, non destinato alla vendita o all'uso continuativo. In caso di vendita a scopo commerciale saranno da integrare tutti i dispositivi di sicurezza descritti nelle norme vigenti nella data di revisione e modifica del prototipo successiva a quella descritta da questo manuale.

## 1.1 Dati di targa

Componente | Tipo | Parametri Principali | Note per il Manuale
BC547 | Transistor BJT NPN | Vceo: 45V | Ic: 100mA | hFE: 110-800 | Ptot: 500mW | Amplificazione piccoli segnali o interruttore per bassi carichi.
LM311 | Comparatore di Tensione | Vcc: 5V-30V | Out: 50mA | Tempo risposta: 200ns | Uscita Open Collector: richiede resistenza di pull-up esterna.
MP1584 | Modulo Step-Down (Buck) | Vin: 4.5V-28V | Vout: 0.8V-20V | Iout: 2A (3A picco) | Regolare il trimmer Vout PRIMA di collegare il carico. Switching 1.5MHz.
ESP32-S3 N16R8 | Microcontrollore | CPU: 240MHz Dual-Core | 16MB Flash | 8MB PSRAM | 3.3V | Logica operativa 3.3V (NON tollerante 5V). WiFi/BT integrati.
SFH309 | Fototransistor (IR) | Peak: 860nm | Vce: 35V | Ic: 15mA | Ricevitore sensibile alla luce infrarossa. Uso in coppie ottiche.
TSAL4400 | LED Infrarosso | Peak: 940nm | If: 100mA | Vf: 1.35V | Emettitore IR. Non visibile a occhio nudo. Necessaria resistenza serie.
DRV8825 | Driver Stepper | Vm: 8.2V-45V | Iout: 1.5A-2.5A | Microstepping: 1/32 | CRITICO: Tarare VREF prima dell'uso. Installare dissipatore termico.
AH49E | Sensore di Hall Lineare | Vcc: 3.0V-6.5V | Sensibilità: 1.4-2.1 mV/G | Out: Analogica | Output raziometrico. Rileva intensità e polarità del campo magnetico.
42BYGHW811 | Motore Stepper NEMA 17 | Passo: 1.8° | Corrente: 2.5A/fase | Coppia: 4.8 kg·cm | Motore bipolare 4 fili.

# 2. IDENTIFICAZIONE DELLA MACCHINA

## 2.1 Disegno Prototipo

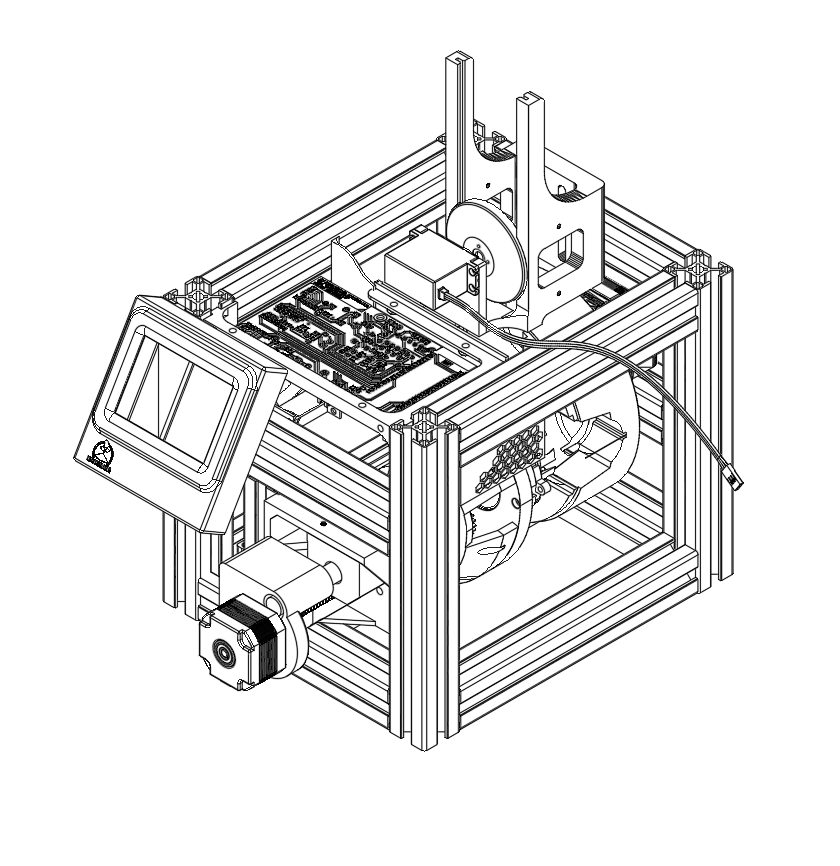
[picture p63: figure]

2

1

3

10

8

TABELLA COMPONENTI
N° | DESCRIZIONE
1 | Profili in alluminio 30X30 cm
2 | Magazzino verticale capsule
3 | paratia di selezionatura servo attivata del magazzino verticale
4 | Tamburo di posizionamento
5 | Zona di Punzonatura e Raschiatura
6 | Motore passo-passo del Punzone e Raschiatore
7 | Display dell’interfaccia uomo-macchina (HMI)
8 | Scheda elettronica
9 | Griglia di protezione parte elettronica
10 | Ventola di raffreddamento (lato sinistro del macchinario)

7

4

9

6

5

## 2.2 Descrizione Generale:

- Nasce dall'idea di suddivisione automatica delle capsule da caffè, suddivide l’involucro delle capsule in materiale plastico o alluminio dal contenuto in due contenitori distinti;
- È costituita da 3 macro aree:
1. Inserimento e Stoccaggio capsule: magazzino verticale per le capsule da trattare.
2. Tamburo di Posizionamento: sistema di prelievo e gestione delle fasi di punzonatura, raschiatura ed espulsione.
3. Stoccaggio dei due prodotti: due contenitori distinti per involucro e polvere di caffè.
- Inoltre ha altre due componentistiche:
1. Zona di controllo prototipo: Sezione dedicata all’elettronica di controllo del macchinario;
2. Interfaccia uomo-macchina: Sezione dedicata all’interazione tra l’utente e il macchinario tramite un display touch.

Il Decapsulator è un sistema progettato per la separazione del caffè esausto dal suo involucro. Il sistema si articola in tre moduli principali:

- Modulo di Controllo: gestisce i movimenti dei motoriduttori, monitora i sensori di posizione (finecorsa), memorizza i dati operativi della sessione (numero capsule elaborate, log di funzionamento) e fornisce un'interfaccia dedicata al controllo da parte dell’utente e tools utili per la manutenzione.
- Modulo Operativo: sistema di movimento con il tamburo di posizionamento e poi estrazione del caffè tramite la punzonatura e la raschiatura;
- Compatibilità: Il sistema è compatibile con capsule Dolce Gusto (NESCAFÉ).

## 2.3 Destinazione d'uso:

Il progetto si rivolge a chi desidera abbattere i costi di smaltimento dei rifiuti secchi, automatizzando la separazione delle capsule esauste. Permette di recuperare la plastica per il riciclo e il caffè come fertilizzante naturale per il proprio eventuale orto o giardino.

## 2.4 INFORMAZIONE SULLA SICUREZZA

Trattandosi di un prototipo sviluppato esclusivamente per finalità didattiche e non destinato all'immissione sul mercato, il sistema non integra la totalità dei dispositivi di sicurezza richiesti per l'uso pubblico o professionale. Pertanto, è stata redatta un’analisi dei rischi residui volta a istruire l’utente sulle corrette modalità operative. Resta inteso che, per un eventuale passaggio alla fase commerciale, il macchinario dovrà essere adeguato alle normative vigenti in materia di sicurezza in data di revisione e deve essere certificato secondo gli standard di compatibilità elettromagnetica e sicurezza domestica.

## 2.5 Rischi Residui

Sicurezza e Analisi dei Rischi:

1. Rischio Schiacciamento/Taglio (Tamburo/Punzone):

Rischio:

Schiacciamento, trascinamento o lieve cesoiamento delle dita e degli arti superiori, dovuto all’inserimento di essi nella zona di lavorazione del tamburo, del punzone e della paratia.

Provvedimento:

- Distanza di Sicurezza: È severamente vietato introdurre le mani o oggetti (cacciaviti, pinze) all'interno della zona di movimento del tamburo mentre il prototipo è alimentato;
- Protezioni Fisiche: Non rimuovere o manomettere le scocche protettive che impediscono l'accesso alle parti meccaniche in rotazione;
- Procedura di Sblocco: In caso di inceppamento di una capsula, scollegare l'alimentazione elettrica e attendere che tutte le parti mobili siano completamente ferme prima di procedere alla rimozione manuale;
- Uso di DPI: Durante le operazioni di manutenzione o pulizia del punzone e del raschiatore, indossare guanti protettivi resistenti al taglio (come indicato nella sezione 9.1).
2. Rischio Elettrico:

Rischio:

Sebbene il circuito operi in Bassa Tensione (24V DC), azzera o limita le conseguenze dei rischi di:

- folgorazione
- contatto diretto
- contatto indiretto
- arco elettrico
- corto circuito
- incendio di origine elettrica

Provvedimento:

- Isolamento dell'alimentazione: Prima di qualsiasi intervento di manutenzione, pulizia o regolazione meccanica, è obbligatorio scollegare fisicamente l'alimentatore dalla presa di rete elettrica.
- Integrità dei cavi: Prima di ogni utilizzo, verificare visivamente che il cavo dell'alimentatore e i cablaggi interni non presentino tagli, abrasioni o fili scoperti. In caso di danni, non accendere la macchina.
- Ambiente di lavoro: Il prototipo deve essere utilizzato esclusivamente in ambienti asciutti. È severamente vietato toccare l'apparato o l'alimentatore con le mani bagnate o in presenza di umidità eccessiva.
- Accesso ai componenti: Non rimuovere le coperture protettive della scheda elettronica e dei driver durante il funzionamento per evitare contatti accidentali che potrebbero causare cortocircuiti o ustioni causati dai driver stessi.
- Protezione da liquidi: Poiché il dispositivo tratta residui organici (fondi di caffè), prestare la massima attenzione affinché eventuali fuoriuscite di liquido non entrino in contatto con la scheda elettronica o i motori.
- Uso di DPI: Durante le operazioni di manutenzione o pulizia del punzone e del raschiatore, indossare guanti protettivi resistenti al taglio (come indicato nella sezione 9.1).
3. Rischio Incendio ed Esplosione:

Rischio:

Il macchinario è provvisto di una pila 9V al Li-MnO2 (Litio diossido di manganese)

la quale se soggetta a fonti di calore, se danneggiata o bagnata potrebbe

innescare un’esplosione e/o un incendio.

I motoriduttori e i driver con cui sono azionati possono scaldare e generare degli

incendi nonostante essi siano protetti internamente da una protezione termica in

caso di sovracorrenti e temperature troppo elevate, i quali bloccano anche il

movimento dei motori e causano il macchinario ad andare in protezione.

Provvedimento:

- Ventilazione e Raffreddamento: Non coprire le feritoie di ventilazione o la ventola di raffreddamento dei driver. Assicurarsi che ci siano almeno 10 cm di spazio libero attorno all'area dell'elettronica.
- Manutenzione Elettrica: Verificare periodicamente che i morsetti dei cavi sui driver (DRV8825) e sulla scheda ESP32 siano ben serrati. Cavi allentati possono generare archi elettrici o surriscaldamenti.
- Pulizia Residui: Rimuovere quotidianamente la polvere di caffè o residui organici che potrebbero accumularsi vicino ai motori o ai circuiti. Il caffè secco è un materiale combustibile.
- Sorveglianza: Trattandosi di un prototipo didattico, la macchina non deve mai essere lasciata in funzione senza supervisione. In caso di assenza, scollegare fisicamente il cavo di alimentazione.
- Protezione Elettrica: Assicurarsi che la linea elettrica a cui viene collegato l'alimentatore sia protetta da un interruttore magnetotermico e differenziale (salvavita) a norma.

Non esporre a fonti di calore e non bagnare il macchinario

4. Rischio Chimico Secondario:

Rischio:

Rischio chimico secondario derivante da danneggiamento o incendio della

pila 9V al Li-MnO2.

In caso di danneggiamento, perforazione o incendio della batteria primaria al

litio-diossido di manganese, può verificarsi la fuoriuscita di elettrolita e la

liberazione di vapori irritanti o corrosivi per pelle, occhi e vie respiratorie.

Provvedimento:

- Integrità della Batteria: È vietato forare, schiacciare, smontare o sottoporre a forti urti la batteria da 9V. Un danno meccanico all'involucro è la causa primaria di fuoriuscita di sostanze chimiche.
- Protezione Termica: Non esporre il prototipo e la relativa batteria a temperature superiori a 60°C o a fonti di calore diretto (raggi solari prolungati, radiatori). Il calore può causare il "gonfiore" della batteria e la rottura delle guarnizioni di tenuta.
- In caso di perdita di liquido (Elettrolita):
1. Evitare il contatto diretto con la pelle e gli occhi.
2. Indossare guanti in nitrile e occhiali protettivi prima di maneggiare una batteria danneggiata.
3. Pulire eventuali residui sulla macchina con un panno assorbente asciutto, operando in un ambiente molto ventilato.
- In caso di inalazione di vapori: Se la batteria dovesse emettere fumo o odori pungenti, spegnere la macchina (se sicuro farlo), allontanarsi immediatamente e ventilare il locale per almeno 30 minuti.
- Primo Soccorso:
1. Contatto cutaneo: Lavare abbondantemente con acqua e sapone.
2. Contatto oculare: Risciacquare con acqua corrente per almeno 15 minuti e consultare un medico.
- Stoccaggio e Sostituzione: Utilizzare solo batterie di alta qualità e verificare che i contatti non presentino tracce di ossidazione. Rimuovere la batteria se il prototipo non viene utilizzato per lunghi periodi.

## 2.6 Tabella dei rischi

SIMBOLO | SIGNIFICATO | DESCRIZIONE
| Marchio CE | Indica che il prototipo è stato progettato tenendo conto dei requisiti essenziali delle Direttive Europee applicabili.
| Pericolo di schiacciamento / intrappolamento | Mantenere le mani a distanza di sicurezza dagli organi in movimento. Non rimuovere le protezioni fisse.
| Rischio elettrico | Togliere tensione prima di eseguire qualsiasi intervento. Accesso consentito solo a personale qualificato.

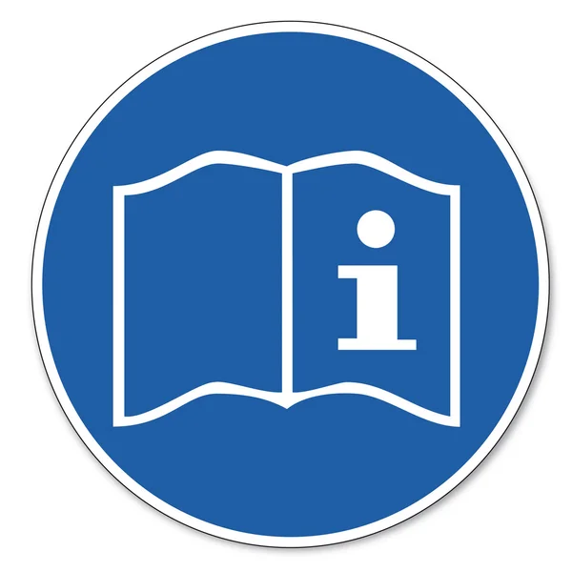
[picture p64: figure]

| Obbligo lettura Manuale | Indica che è obbligatorio leggere e comprendere integralmente le istruzioni prima di operare, installare o fare manutenzione sul sistema.

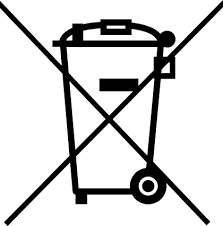
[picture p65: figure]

| Smaltimento RAEE (Rifiuti Elettronici) | Indica che i componenti elettrici ed elettronici del sistema non devono essere smaltiti nei rifiuti generici.
| Rischio di Temperatura | Non esporre la batteria a temperature superiori a 60°C. Evitare il posizionamento vicino a fonti di calore o alla luce diretta del sole.
| Rischio di esplosione | Non gettare nel fuoco, non forare e non tentare di ricaricare la batteria (se non specificatamente indicato come ricaricabile).
| Rischio d’incendio | In caso di cortocircuito o danneggiamento fisico, le celle al litio possono innescare una reazione termica. Tenere lontano da materiali infiammabili (carta, plastica, tessuti). Non tentare di estinguere un eventuale incendio con acqua; utilizzare estintori a polvere o CO2.
| Rischio Chimico | Rilascio di sostanze corrosive e nocive per la pelle

# 3. TRASPORTO E DIMENSIONI

CARATTERISTICA | VALORE
Larghezza | 286 mm
Lunghezza | 596 mm
Altezza | 520 mm
Peso | 7 kg

Istruzioni di trasporto:

Proteggere il sistema dagli urti. Scollegare tutte le alimentazioni prima del trasporto. Proteggere le parti elettroniche da umidità e vibrazioni. Mantenere il dispositivo rivolto verso l'alto, scollegare la pila posta sul retro del macchinario per evitare danneggiamenti e i potenziali rischi che comporta, riferimento alla sezione di rischi e pericoli.

# 4. REGOLE GENERALI PER L’USO DELLA MACCHINA

Leggere attentamente il libretto di istruzioni.

La macchina deve essere allacciata ad una regolare presa di corrente. La macchina deve essere mantenuta pulita. La manutenzione va eseguita a macchina spenta.

IMPORTANTE: Mai immergere la macchina o le sue componenti rimovibili in acqua o introdurla in lavastoviglie.

NOTA: La macchina è compatibile esclusivamente con capsule Dolce Gusto (NESCAFÉ).

## 4.1 Istruzioni d’uso

1. Assicurarsi che l’interruttore posto sul retro del macchinario sia nella posizione di OFF;
2. Verificare che tutte la protezione siano correttamente fissate e che la copertura laterale sia ben serrata;
3. Collegare alla presa della corrente;
4. Impostare l’interruttore posto sul retro del macchinario sulla posizione di ON;
5. Aspettare che il macchinario finisca l’inizializzazione (pic. 1.1) e di non interferire con le parti in movimento;
6. Una volta conclusa l’inizializzazione (pic. 1.2) e avvenuto il cambio alla schermata principale (pic. 2.1), caricare le capsule all’interno del magazzino verticale (max. 3);
7. Premere il pulsante di START al centro del display (pic. 2.1);
8. In caso di emergenza premere il tasto di STOP (pic. 2.2);
9. Verificare i messaggi che compaiono sul display durante il ciclo di lavorazione, in caso di errori, necessità di svuotare le capsule o interazioni richieste dalla parte dell’utente e dopo aver visionato il messaggio premere “OK” (pic. 2.3). In caso di errori gravi verrà chiesto di attendere e comunque verrà eseguito un Homing qualora l’errore fosse stato risolto e dopo aver premuto “OK” per poter garantire il corretto posizionamento dei motori.
10. Per consultare il manuale d’uso digitale, premere il pulsante “manuale d’uso” e scansionare il codice QR (pic. 2.4).

## 4.2 Istruzioni d’uso interfaccia utente

1. Schermata Avvio Macchina

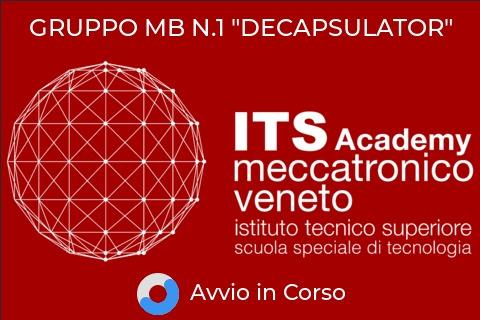
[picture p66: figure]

Pic.1.1 Avvio Macchina (in corso)

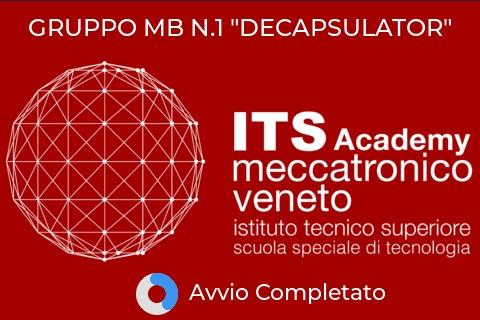
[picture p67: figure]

Pic. 1.2 Avvio Macchina (completato)

2. Schermata Principale

Pic.2.1 Schermata Principale (macchina Ferma)

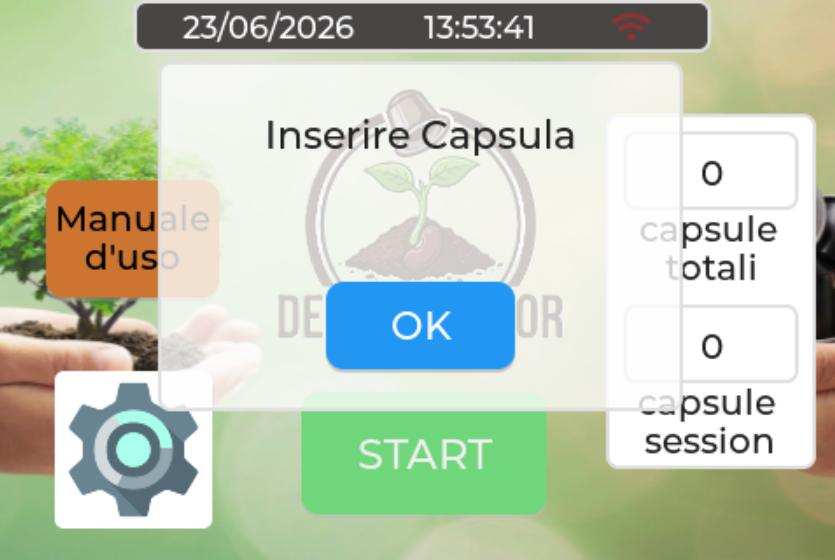
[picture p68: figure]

Pic.2.3 Schermata Principale (presenza errore)

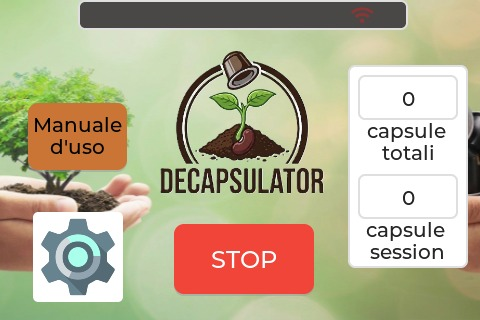
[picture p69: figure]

Pic.2.2 Schermata Principale (macchina in movimento)

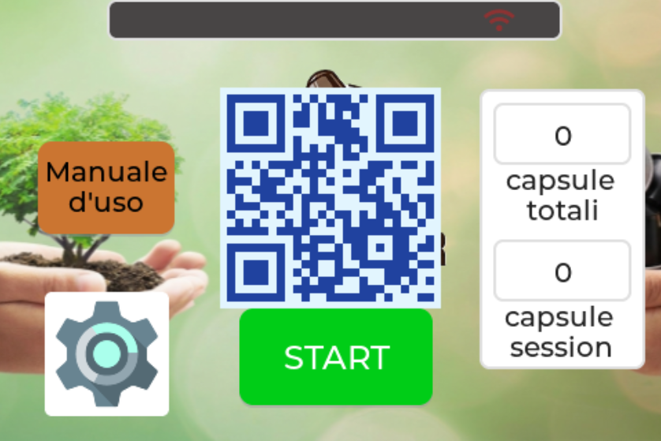
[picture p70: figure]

Pic.2.4 Schermata Principale (QR Manuale d’uso)

# 5. INSTALLAZIONE MACCHINA

## 5.1 Installazione dell’apparecchio

Leggere attentamente le istruzioni.

- Non installare mai la macchina in un ambiente che può raggiungere una temperatura inferiore o uguale a 0°C (se l’acqua si ghiaccia, l’apparecchio può danneggiarsi) o superiore a 40°C.
- Verificare che la tensione della rete elettrica corrisponda a quella indicata nella targa dati dell’apparecchio.
- In caso di incompatibilità tra la presa di corrente e la spina dell’apparecchio, fare sostituire la spina dell’alimentatore con un’altra di tipo adatto.
- Posizionare l’apparecchio sopra un piano di lavoro lontano da rubinetti dell’acqua e lavelli e fonti di calore.
- Dopo aver tolto l’imballaggio, assicurarsi dell’integrità dell’apparecchio prima della sua installazione.
- Non lasciare alla portata dei bambini i materiali utilizzati per imballare la macchina.

## 5.2 Cablaggi principali:

Per il corretto funzionamento, effettuare i seguenti collegamenti:

- Alimentazione: collegare il cavo di alimentazione al connettore posto sul retro del dispositivo. Verificare che il connettore sia completamente inserito prima di avviare il sistema.

# 6 Pulizia dell’apparecchio

Leggere attentamente le istruzioni.

- Obbligatorio disinserire la spina dall’impianto elettrico quando si esegue la pulizia.
- Lasciare raffreddare l’apparecchio prima della pulizia per evitare ustioni.
- Estrarre il serbatoio del caffè e delle capsule.
- Pulire la carrozzeria e gli accessori con un panno umido ed asciugare successivamente con un panno asciutto non abrasivo. È sconsigliato l’uso di detergenti.
- Non sottoporre l’apparecchio ad abbondanti getti d’acqua o ad immersioni parziali o totali.
- È consigliato lavare giornalmente il serbatoio e il suo coperchio e riempirlo con acqua fresca potabile.
- È consigliato pulire le altre parti a contatto diretto con il cibo o che possono venire in contatto con acque reflue, almeno una volta alla settimana.

# 7 Gestione delle Criticità e Guasti

## 7.1 In caso di guasto dell’apparecchio

Non utilizzare l’apparecchio nel caso in cui il cavo o la spina siano danneggiati, dopo un malfunzionamento della macchina o dopo un danno di qualunque natura. Portare l’apparecchio al più vicino centro di assistenza autorizzato per un controllo, riparazione o una verifica sul corretto funzionamento. Se il cavo d’alimentazione è danneggiato, deve essere cambiato dal produttore o dal suo servizio assistenza. In caso di guasto o di cattivo funzionamento dell’apparecchio, spegnerlo e non manometterlo.

Per eventuali riparazioni, rivolgersi solamente ad un Centro di Assistenza Tecnica autorizzato dal costruttore e richiedere l’utilizzo di ricambi originali. Il mancato rispetto di quanto sopra può compromettere la sicurezza dell’apparecchio e fare perdere il diritto alla garanzia.

## 7.2 Uso improprio dell’apparecchio

Il costruttore non può essere considerato responsabile per eventuali danni derivanti da usi impropri, erronei ed irragionevoli.

ATTENZIONE: CONSERVARE QUESTE ISTRUZIONI

# 8. ALIMENTAZIONE ELETTRICA

## 8.1Istruzioni per il cavo di alimentazione

a) È possibile utilizzare prolunghe a condizione che si presti particolare attenzione durante l’uso.
b) Qualora venga utilizzata una prolunga:
1. Verificare che la potenza elettrica della prolunga sia almeno pari a quella dell’apparecchio;
2. Posizionare il cavo più lungo in modo tale che non penda dal piano di lavoro o dal tavolo per evitare che i bambini lo tirino o inciampino.

Il sistema utilizza un sistema di alimentazione:

- Alimentatore principale esterno: 24V — 3A —72W.
- Alimentazione di backup per salvataggio dati: batteria interna da 9 V — 1,2 Ah al litio diossido di manganese (Li-MnO₂), la quale copre un ruolo non fondamentale se non per salvare i dati delle capsule.

La batteria deve essere alloggiata nell'apposito scomparto prima dell'accensione.

NOTA: Controllare regolarmente il livello di carica della batteria di backup per garantire un funzionamento ottimale del sistema in caso di interruzione dell'alimentazione principale.

# 9. SICUREZZA E MANUTENZIONE

## 9.1 Dispositivi di Protezione Individuale (DPI)

Durante la messa in servizio e le operazioni di manutenzione è obbligatorio l'utilizzo dei seguenti DPI:

- Guanti da lavoro: per prevenire tagli o lesioni meccaniche durante l'interazione con le parti metalliche e mobili.
- Indumenti protettivi: Abiti o grembiuli che non limitino il movimento, resistenti ai tagli e che non permettano l’impigliamento.

In caso vi sia la necessità di maneggiare la pila 9V al Li-MnO2 danneggiata è obbligatorio utilizzare anche i seguenti DPI:

- Occhialini protettivi: Per prevenire lesioni e irritazioni.
- DPI per le vie respiratorie: Mascherine o respiratori con filtri appropriati, poiché le batterie danneggiate possono rilasciare gas nocivi o polveri irritanti durante la movimentazione.
- Indumenti protettivi: Abiti o grembiuli che non limitino il movimento e che siano resistenti agli acidi/sostanze chimiche per proteggere la pelle e i vestiti da contaminazioni.
- Note di sicurezza operativa:
    1. Assicurarsi che il macchinario sia spento e scollegato dalla rete elettrica prima di ogni intervento
    2. è estremamente consigliato allontanare la pila di almeno 2,5 - 5 metri da sostanze o componenti combustibili per limitare la propagazione di un possibile incendio innescato dalla pila danneggiata.
    3. Evitare interventi in luoghi chiusi e poco arieggiati per evitare l’inalazione di fumi dannosi e irritanti.

NOTA: In caso di malfunzionamenti non risolvibili dall'utente, interrompere immediatamente l'operazione e contattare il servizio di assistenza tecnica prima di procedere con qualsiasi altra azione sul macchinario.

## 9.2 Precauzioni di Sicurezza

- Tenere le parti di piccole dimensioni fuori dalla portata dei bambini (rischio di soffocamento).
- Spegnere e scollegare l'alimentatore quando il sistema non è in uso, per prevenire surriscaldamenti e rischi elettrici.
- Non utilizzare il dispositivo in ambienti umidi o bagnati.
- Utilizzare i Dispositivi di Protezione Individuale (DPI) richiesti

## 9.3 Manutenzione Periodica

ATTIVITÀ | DESCRIZIONE
Pulizia | Rimuovere i residui di polvere con un panno in microfibra. Per una pulizia più profonda, è possibile sciacquare le parti non elettroniche con acqua.
Ispezione | Verificare periodicamente lo stato dei cavi elettrici e l'assenza di ostacoli nelle parti mobili, di residui di polvere di caffè e/o plastiche incastrate.

## 9.4 Manutenzione tramite pagina di diagnostica sull’interfaccia utente

Per aiutare il manutentore ad individuare problemi è possibile ottenere dei privilegi elevati attraverso un login e di conseguenza accedere alla pagina di diagnostica composta dal registro eventi (Log) del macchinario, dal movimento manuale (Jog) dei motori passo-passo del tamburo rotante e del punzone, calibrazione touch schermo e le impostazioni WiFi.

Come accedervi:

Passo 1: Individuare nella pagina principale l’icona dell’ingranaggio indicata in figura

(pic. 3.1)

Passo 2: Inserire la password unica fornita ai manutentori specializzati (pic. 3.2)

Pic.3.1 Puls. impostazioni

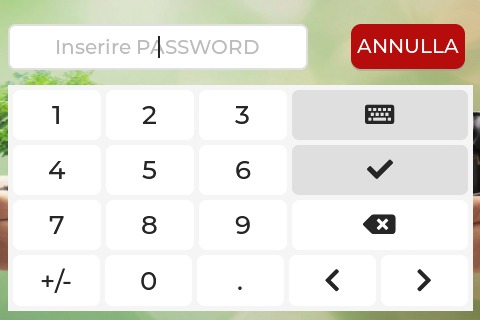
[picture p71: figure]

Pic. 3.2 Password diagnostica

## 9.5 Accesso alla pagina del logger la visione messaggi di diagnostica.

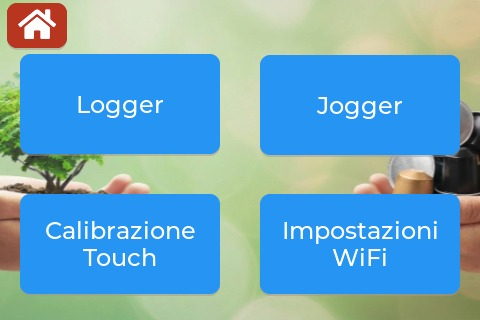
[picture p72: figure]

Pic 4.1

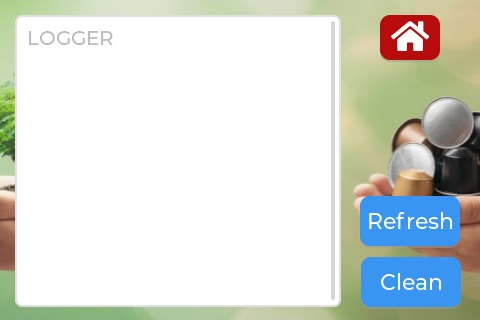
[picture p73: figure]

Pic 4.2 Pagina Logger

“Refresh”= ricarica la lista con i messaggi più recenti

“Clean”= Cancella tutta la lista dei messaggi diagnostica

## 9.6 Accesso alla pagina di Jogger per il movimento manuale dei motori.

Pic 5.1 (accesso al Jogger)

Passo 1: Una volta entrati nella pagina di diagnostica è possibile accedere alla pagina di Jogger esclusivamente se non si è avviato il processo automatico precedentemente e bisognerà aspettare che questo termini o che sia messo in STOP prima di accedervi. Vedere (Pic. 5.2)

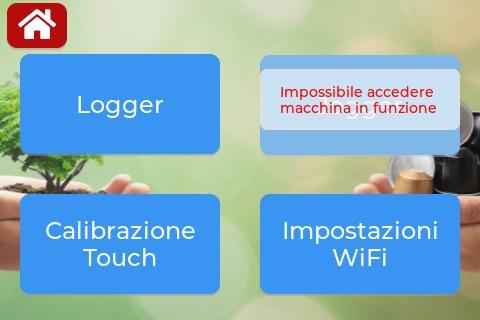
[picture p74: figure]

Pic 5.2 (accesso negato al Jogger col macchinario in funzione)

Passo 2: Una volta effettuato l’accesso alla pagina si presenterà l’interfaccia rappresentata in foto (Pic. 6.1).

Pic 6.1 (interfaccia iniziale del Jogger)

Abilitazione Motori: I motori vanno abilitati con il tasto “ABILITA” (Pic. 63.2) per poter essere comandati.

Homing non disponibile

Pic 6.2 (abilitazione dei motori)

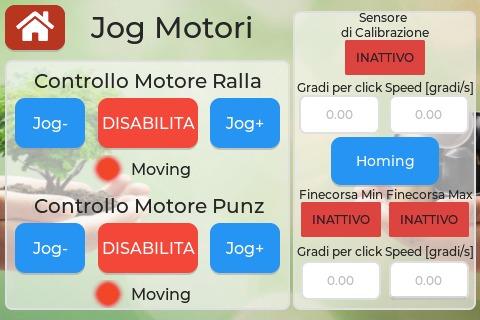
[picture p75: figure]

Homing disponibile

Pic 6.3 (entrambi i motori abilitati, da qui è possibile fare Jog- e Jog+ oppure eseguire l’Homing)

Configurazione Motori: Prima di eseguire un movimento tramite Jog- o Jog+ è necessario impostare i “Gradi per click” ovvero lo spostamento del motore ogni volta che viene premuto il tasto Jog- o Jog+ e la “Speed” voluti. La velocità massima dei motori è di 900°/s e la corsa del Punzone da Finecorsa Min a Finecorsa Max è di circa 30mm lineari ovvero circa 15 giri (5400°), assicurarsi che durante il movimento del punzone non vi sia una collisione con il tamburo (Ralla).

I dati dei valori minimi e massimi di configurazione vengono riportati nella seguente tabella:

Valore | Gradi per Click Tamburo | Speed [gradi/s] Tamburo | Gradi per Click Punzone | Speed [gradi/s] Punzone
Min | 1.8° | 0.0°/s | 1.8° | 0.0°/s
Max | [(9.22337E+18) - 1]° | 900°/s | 5400° | 900°/s

NOTA: I dati di configurazione non influiscono con le velocità di Homing.

NOTA: I dati impostati non tengono conto delle riduzioni, è da considerare una riduzione di 1/3 per il tamburo (ralla) (es. 3 giri motore = 1 giro tamburo) e di 2mm lineari per giro (360°) nel caso del punzone (es. 5 giri motore = 10mm punzone). Premere sulla casella in cui si vuole cambiare il valore.

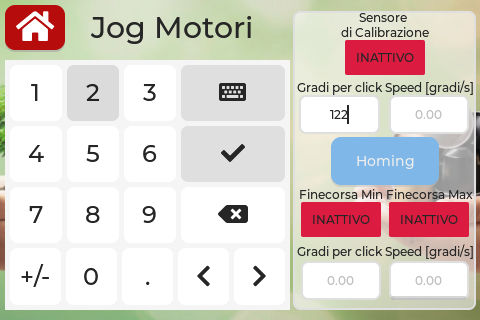
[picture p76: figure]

Premere la casella di testo per poter cambiare tramite il tastierino numerico

Pic 6.4 (Selezione dei parametri di spostamento e velocità)

Movimento con tasti Jog- e Jog+: Il tasto Jog- (Pic 6.5) muoverà il motore in direzione antioraria osservando quest’ultimo ponendo la fine dell’albero di fronte a noi, Jog+ (Pic 6.6) invece in direzione oraria.

NOTA: Durante qualsiasi movimento verranno illuminati i LED accanto alla parola “Moving” di verde. Se il motore è fermo invece rimarrà rosso.

NOTA: Premere più volte Jog- e Jog+ fa accumulare i movimenti fino ad un massimo di 5 movimenti.

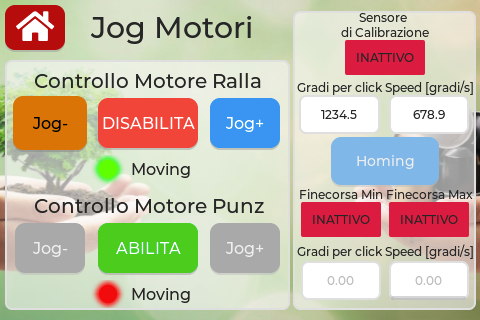
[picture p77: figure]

Pic 6.5 (pulsante Jog- premuto, movimento in senso antiorario)

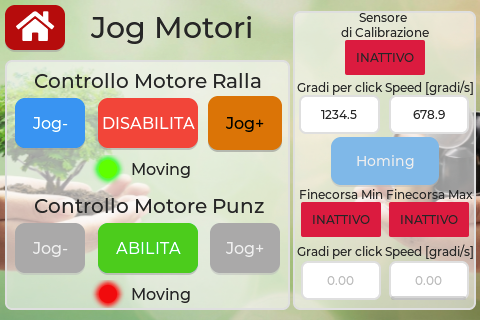
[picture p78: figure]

Pic 6.6 (pulsante Jog+ premuto, movimento in senso orario)

Homing: Inizialmente o ogni qual volta vi sia la necessità di portare i motori in una posizione certa è consigliato eseguire l’Homing portando così i motori in posizione iniziale per evitare danneggiamenti al macchinario. Per fare ciò abilitare entrambi i motori (altrimenti non sarà permesso l’Homing) come indicato in figura (Pic. 6.6), dopodichè premere il tasto “Homing” indicato in figura (Pic. 6.3) e i motori si muoveranno con una velocità preimpostata per eseguire quest’azione.

NOTA: Per abortire l’Homing sarà necessario dover ripremere il tasto “Homing”.

NOTA: Durante l’Homing non sarà possibile né premere i tasti “Jog-”, “Jog+”, “Disabilita” né impostare “Gradi per click” né “Speed [gradi/s]” di entrambi i motori ma saranno comunque visibili gli stati dei sensori durante tutti i movimenti dei motori.

NOTA: Durante l’Homing verranno illuminati i LED accanto alla parola “Moving” di verde. Se il motore è fermo invece rimarrà rosso.

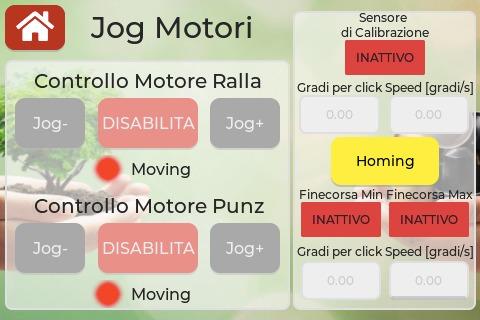
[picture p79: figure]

Pic 6.7 (Homing con pulsante intermittente giallo-arancione)

## 9.6 Accesso alla pagina di impostazioni WiFi

Pic 7.1 Accesso alle impostazioni wifi

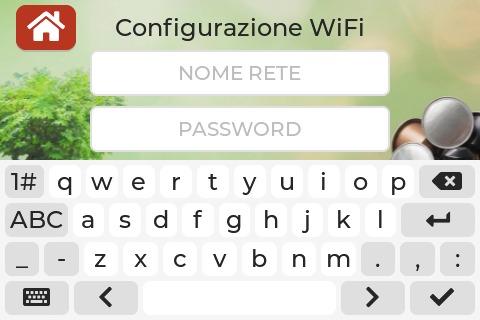
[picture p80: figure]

pic. 7.2 Schermata impostazioni WiFi

Connessione WiFi: Per collegarsi alla connessione WiFi premere le caselle, nome rete e password e utilizzando la tastiera in basso inserire il nome della rete e la password (pic. 7.2)

# 10. GESTIONE DELLE EMERGENZE

In caso di blocco o anomalia:

- Stop Immediato: Interrompe ogni comando di movimento all’apertura del pannello, assicurarsi che i fusibili non siano rimasti nel portafusibili;
- Spegnimento: Disattivare l'alimentazione generale;
- Analisi: Identificare l'ostacolo o il guasto meccanico prima di riavviare.

# 11. REGISTRO DELLE MANUTENZIONI

Componente | Tipo di Intervento | Frequenza | Metodo
Vasca Residui Organici | Svuotamento e lavaggio | Ogni 10 cicli | Acqua e sapone neutro
Tamburo di Posizionamento | Rimozione polvere incrostata | Mensile | Pennello a setole dure o aria compressa
Punzone e Raschiatore | Verifica residui plastici | Mensile | Panno umido in microfibra
Ventola Raffreddamento | Controllo ostruzione polvere | Mensile | Aspirazione esterna

# 12. SMALTIMENTO

Al termine della vita utile del prodotto, seguire le istruzioni di smaltimento riportate di seguito nel rispetto delle normative ambientali vigenti.

## 12.1 Procedura di Smantellamento

- Rimuovere la batteria di backup dal suo alloggiamento prima di qualsiasi altra operazione.
- Identificare i componenti riutilizzabili o recuperabili: motori, schede elettroniche, profili strutturali, sensori, alimentatore.

## 12.2 Riciclaggio dei Materiali

MATERIALE | DESTINAZIONE
Plastica / Alluminio | Raccolta differenziata secondo le normative locali.
Componenti Elettronici (RAEE) | Conferire presso centri di smaltimento autorizzati per rifiuti elettronici (RAEE).
Batteria Li-MnO₂ | Smaltimento speciale presso punto di raccolta batterie esauste (non nei rifiuti urbani).

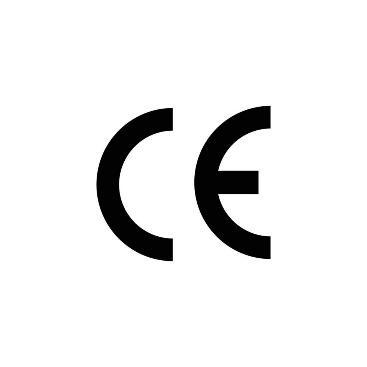
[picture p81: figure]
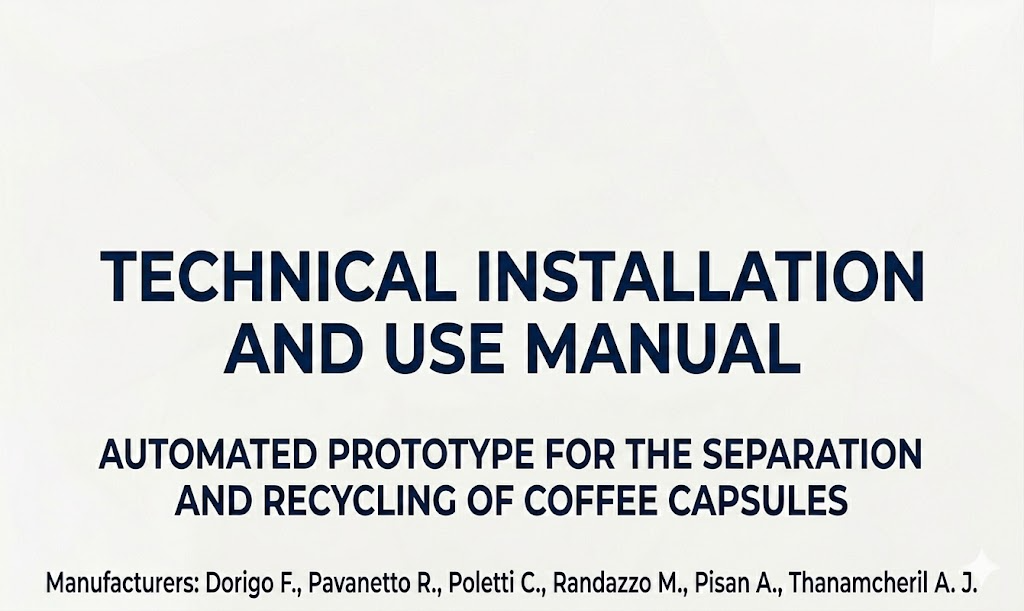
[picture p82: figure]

Headquarters:

Via Sansovino, 6, 31044 Montebelluna TV

Via Avenale, 6, 31033 Castelfranco Veneto TV

" This technical documentation was designed to guide the operator in interacting with the DECAPSULATOR prototype, a system born from an in-depth educational development focused on construction accuracy and functional efficiency. The guidelines reported here are essential for exploring the potential of the device, while ensuring the maintenance of the highest operational safety standards. Given the experimental and academic nature of the project, it is imperative to operate under constant supervision and strictly adhere to the procedures outlined, as the development team disclaims any responsibility for improper or non-prescribed uses. For us, the correct management of the system represents the final validation of the path undertaken during the school year."

# 1. EC declaration of conformity

CE declaration in original language.

This manual is an integral part of the product and must be kept for its entire life.

This prototype was designed following the safety criteria of the various directives:

- Machinery Directive 2006/42/EC: Applicable as the device features moving parts, including a rotating drum, servo-activated sorting bulkhead and punch, which pose mechanical risks.
- Low Voltage Directive (LVD) 2014/35/EU: Consulted for the safety of electrical components and power circuits.
- Electromagnetic Compatibility (EMC) Directive 2014/30/EU: Applicable to ensure that electronics do not interfere with other equipment surrounding the machinery.
- RoHS Directive 2011/65/EU: Consulted to ensure the absence of hazardous substances in electronic components and filler materials.

These standards were used for calculations, mechanical sizing and definition of 2D/3D drawings:

- UNI EN ISO 12100:2010: Machinery safety - General design principles - Risk assessment and mitigation.
- UNI EN ISO 13857:2020: Safety distances to prevent reaching dangerous areas with the upper limbs (used to size the capsule mouth and drum casings).
- UNI EN ISO 14119:2013: Interlocking devices associated with shelters (used for choosing and installing the safety micro-switch on the lid).
- CEI EN 60204-1: Safety of electrical equipment of machines (used for the electrical and functional diagram).

NOTE: Intended for use: Prototype for educational purposes, not intended for sale or continuous use. In the case of sale for commercial purposes, all the safety devices described in the rules in force on the date of revision and modification of the prototype following that described by this manual will have to be integrated.

## 1.1 Plate data

Componente | Tipo | Parametri Principali | Note per il Manuale
BC547 | Transistor BJT NPN | Vceo: 45V | Ic: 100mA | hFE: 110-800 | Ptot: 500mW | Amplification of small signals or switches for low loads.
LM311 | Comparatore di Tensione | Vcc: 5V-30V | Out: 50mA | Tempo risposta: 200ns | Open Collector Output: Requires external pull-up resistance.
MP1584 | Modulo Step-Down (Buck) | Vin: 4.5V-28V | Vout: 0.8V-20V | Iout: 2A (3A picco) | Adjust the Vout trimmer BEFORE connecting the load. Switching 1.5MHz.
ESP32-S3 N16R8 | Microcontrollore | CPU: 240MHz Dual-Core | 16MB Flash | 8MB PSRAM | 3.3V | 3.3V operating logic (NOT tolerant 5V). Built-in WiFi/BT.
SFH309 | Fototransistor (IR) | Peak: 860nm | Vce: 35V | Ic: 15mA | Receiver sensitive to infrared light. Use in optical pairs.
TSAL4400 | LED Infrarosso | Peak: 940nm | If: 100mA | Vf: 1.35V | IR emitter. Not visible to the naked eye. Serious resistance needed.
DRV8825 | Driver Stepper | Vm: 8.2V-45V | Iout: 1.5A-2.5A | Microstepping: 1/32 | CRITICAL: Tare VREF before use. Install a heat sink.
AH49E | Sensore di Hall Lineare | Vcc: 3.0V-6.5V | Sensibilità: 1.4-2.1 mV/G | Out: Analogica | Raziometric output. Detects magnetic field strength and polarity.
42BYGHW811 | Motore Stepper NEMA 17 | Passo: 1.8° | Corrente: 2.5A/fase | Coppia: 4.8 kg·cm | 4-wire bipolar motor.

# 2. Machine identification

## 2.1 Prototype Design

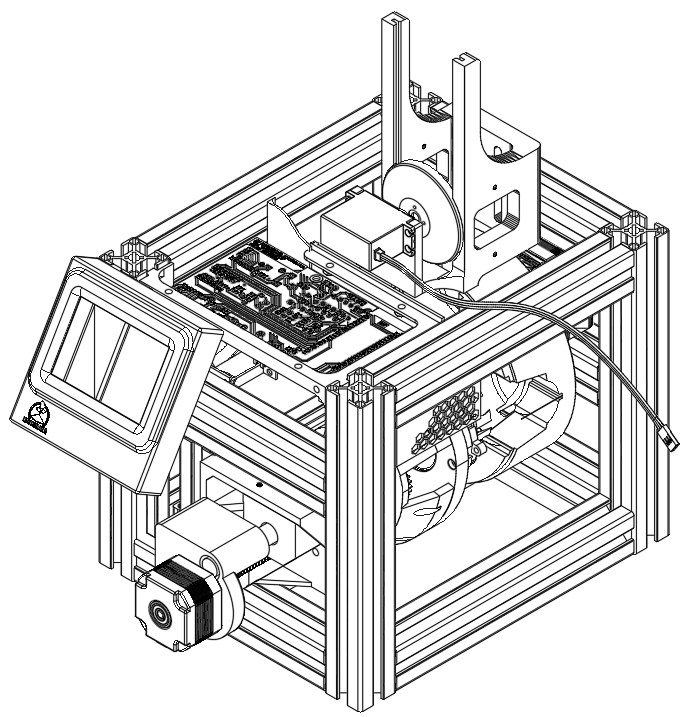
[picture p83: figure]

1

2

3

10

8

COMPONENTS TABLE
N° | DESCRIPTION
1 | Aluminium profiles 30X30 cm
2 | Vertical capsule warehouse
3 | servo-activated sorting bulkhead of the vertical magazine
4 | Positioning drum
5 | Punching and Scraping Area
6 | Punch Stepper Motor and Scraper
7 | Human-Machine Interface (HMI) display
8 | Electronic card
9 | Electronic part protection grid
10 | Cooling fan (left side of the machinery)

7

4

6

9

5

## 2.2 General Description:

- It was born from the idea of automatically dividing coffee capsules, dividing the capsule casing made of plastic or aluminum material with contents into two distinct containers;
- It consists of 3 macro areas:
1. Capsule insertion and storage: vertical warehouse for the capsules to be treated.
2. Positioning Drum: system for picking up and managing the punching, scraping and ejection phases.
3. Storage of the two products: two separate containers for casing and coffee powder.
- It also has two other components:
1. Prototype control area: Section dedicated to machinery control electronics;
2. Human-machine interface: Section dedicated to the interaction between the user and the machine via a touch display.

The Decapsulator is a system designed for separating spent coffee from its casing. The system is divided into three main modules:

- Control Module: Manages gearmotor movements, monitors position sensors (limit switches), stores session operating data (number of capsules processed, operation logs), and provides a dedicated user control interface and useful maintenance tools.
- Operating Module: movement system with the positioning drum and then extraction of the coffee through punching and scraping;
- Compatibility: The system is compatible with Dolce Gusto capsules (NESCAFÉ).

## 2.3 Intended use:

The project is aimed at those who want to reduce the costs of dry waste disposal by automating the separation of used capsules. It allows you to recover plastic for recycling and coffee as a natural fertilizer for your possible vegetable garden or garden.

## 2.4 Information on the security

Since this is a prototype developed exclusively for educational purposes and not intended for marketing, the system does not integrate all the safety devices required for public or professional use. Therefore, a residual risk analysis was drawn up aimed at instructing the user on the correct operating methods. It is understood that, for a possible transition to the commercial phase, the machinery must be compliant with the current safety regulations on the date of inspection and must be certified according to the standards of electromagnetic compatibility and home safety.

## 2.5 Residual risks.

Safety and Risk Analysis:

1. Crush/Cut Risk (Drum/Stick):

Risk:

Crushing, dragging or slight shearing of the fingers and upper limbs, due to their insertion into the working area of the drum, punch and bulkhead.

Measure:

- Safety Distance: It is strictly prohibited to introduce hands or objects (screwdrivers, pliers) into the movement zone of the drum while the prototype is powered;
- Physical Protections: Do not remove or tamper with protective bodies that prevent access to rotating mechanical parts;
- Unlocking Procedure: In the event of a capsule jamming, disconnect the power supply and wait until all moving parts are completely stationary before proceeding with manual removal;
- Use of PPE: During maintenance or cleaning of the punch and scraper, wear protective, cut-resistant gloves (as indicated in section 9.1).
2. Electrical Risk:

Risk:

Although the circuit operates in Low Voltage (24V DC), it eliminates or limits the consequences of the risks of:

- lightning strike
- direct contact
- indirect contact
- electric arc
- short circuit
- fire of electrical origin

Measure:

- Power isolation: Before any maintenance, cleaning or mechanical adjustment, it is mandatory to physically disconnect the power supply from the mains outlet.
- Cable integrity: Before each use, visually check that the power supply cable and internal wiring have no cuts, abrasions or exposed wires. If damaged, do not turn on the machine.
- Working environment: The prototype must be used exclusively in dry environments. It is strictly forbidden to touch the apparatus or power supply with wet hands or in the presence of excessive humidity.
- Component Access: Do not remove the protective covers on the circuit board and drivers during operation to avoid accidental contact that could cause short circuits or burns caused by the drivers themselves.
- Liquid protection: Since the device treats organic residues (coffee grounds), take great care to ensure that any liquid spills do not come into contact with the electronic board or motors.
- Use of PPE: During maintenance or cleaning of the punch and scraper, wear protective, cut-resistant gloves (as indicated in section 9.1).
3. Fire and Explosion Risk:

Risk:

The machine is equipped with a 9V Li-MnO2 (Lithium manganese dioxide) stack

which if subject to heat sources, if damaged or wet could

trigger an explosion and/or fire.

The gearmotors and drivers with which they are driven can heat and generate

fires despite the fact that they are protected internally by thermal protection in

case of overcurrents and excessively high temperatures, which also block the

movement of the engines and cause the machinery to go into protection.

Measure:

- Ventilation and Cooling: Do not cover the ventilation vents or driver cooling fan. Make sure there is at least 10 cm of clearance around the electronics area.
- Electrical Maintenance: Periodically check that the cable clamps on the drivers (DRV8825) and the ESP32 board are tight. Loose cables can generate arcing or overheating.
- Residue Cleaning: Remove coffee dust or organic residue that may accumulate near motors or circuits daily. Dry coffee is a combustible material.
- Surveillance: Since this is an educational prototype, the machine must never be left running unsupervised. In case of absence, physically disconnect the power cord.
- Electrical Protection: Make sure the power line to which the power supply is connected is protected by a standard circuit breaker and differential (lifesaver).

Do not expose to heat sources and do not wet the machinery

4. Secondary Chemical Risk:

Risk:

Secondary chemical risk resulting from damage or fire to the

9V Li-MnO2 stack.

In case of damage, drilling or fire of the primary battery at the lithium-manganese dioxide, electrolyte leakage and release of irritating or corrosive vapors for the skin, eyes and respiratory tract.

Measure:

- Battery Integrity: Drilling, crushing, disassembling or subjecting the 9V battery to severe impacts is prohibited. Mechanical damage to the casing is the primary cause of chemical leakage.
- Thermal Protection: Do not expose the prototype and its battery to temperatures above 60°C or to direct heat sources (extended solar rays, radiators). Heat can cause the battery to "swell" and the seals to break.
- In case of liquid leak (Electrolyte):
1. Avoid direct contact with skin and eyes;
2. Wear nitrile gloves and protective glasses before handling a damaged battery.
3. Clean any residue on the machine with a dry absorbent cloth, operating in a very ventilated environment.
- In case of vapor inhalation: If the battery emits smoke or pungent odors, turn off the machine (if safe to do so), move away immediately and ventilate the room for at least 30 minutes.
- First Aid:
1. Skin contact: Wash thoroughly with soap and water.
2. Eye contact: Rinse with running water for at least 15 minutes and consult a doctor.
- Storage and Replacement: Use only high-quality batteries and check that the contacts show no traces of oxidation. Remove the battery if the prototype is not used for long periods.

## 2.6 Risk Table

Symbol | Meaning | Description
| CE mark | It indicates that the prototype was designed taking into account the essential requirements of the applicable European Directives.
| Crush hazard / entrapment | Keep your hands at a safe distance from moving organs. Do not remove fixed guards.
| Electrical risk | Remove tension before performing any surgery. Access permitted only to qualified personnel.
| Required reading Manual | It indicates that it is mandatory to read and fully understand the instructions before operating, installing or performing maintenance on the system.
| WEEE (Electronic Waste) | It indicates that the electrical and electronic components of the system should not be disposed of in general waste.
| Temperature Risk | Do not expose the battery to temperatures above 60°C. Avoid placement near heat sources or direct sunlight.
| Risk of explosion | Do not throw into the fire, puncture, or attempt to recharge the battery (unless specifically stated as rechargeable).
| Fire risk | In the event of a short circuit or physical damage, lithium cells can trigger a thermal reaction. Keep away from flammable materials (paper, plastic, fabrics). Do not attempt to extinguish any fire with water; use powder or CO2 extinguishers.
| Corrosion risk | Release of corrosive and harmful substances to the skin

# 3. TRANSPORT AND DIMENSIONS

CHARACTERISTIC | VALUE
Width | 286 mm
Length | 596 mm
Height | 520 mm
Weight | 7 kg

Transport instructions:

Protect the system from impacts. Disconnect all power supplies before transport. Protect electronic parts from moisture and vibration. Keep the device facing upwards, disconnect the stack on the back of the machinery to avoid damage and the potential risks it poses, reference to the risks and hazards section.

# 4. GENERAL RULES FOR THE USE OF THE MACHINE

Read the instruction booklet carefully.

The machine must be plugged into a regular power outlet. The machine must be kept clean. Maintenance must be performed with the machine off.

IMPORTANT: Never immerse the machine or its removable components in water or put it in the dishwasher.

NOTE: The machine is only compatible with Dolce Gusto capsules (NESCAFÉ).

## 4.1 Instructions for use

1. Make sure the switch on the back of the machine is in the OFF position;
2. Make sure all the protection is properly secured and that the side cover is tight;
3. Connect to the power outlet;
4. Set the switch on the back of the machine to the ON position;
5. Wait for the machine to finish initialization (pic. 1.1) and not interfere with moving parts;
6. Once initialization is complete (pic. 1.2), and after the screen changes to the main screen (pic. 2.1), load the capsules inside the vertical warehouse (max. 3);
7. Press the START button in the center of the display (pic. 2.1);
8. In case of emergency, press the STOP button (pic. 2.2);
9. Check the messages that appear on the display during the processing cycle, in case of errors, need to empty the capsules or interactions required by the user's side, and after having viewed it press “OK” (pic. 2.3). In case of serious errors, you will be asked to wait and in any case a Homing will be performed if the error has been resolved and after pressing “OK” to ensure the correct positioning of the motors.
10. To consult the digital user manual, press the “user manual” button and scan the QR code (pic. 2.4).

## 4.1 Instructions for use of the user interface

1. Machine starting screen

Pic.1.1 Machine Starting (ongoing)

Pic. 1.2 Machine Starting (completed)

2. Main Screen

Pic.2.1 Main Screen (Machine idle)

Pic.2.3 Main Screen (error present)

Pic.2.2 Main Screen (Machine working)

Pic.2.4 Main Screen (QR user Manual)

# 5. MACHINE INSTALLATION

## 5.1 Installation of the appliance

Read the instructions carefully.

- Never install the machine in an environment that can reach a temperature below or equal to 0°C (if the water freezes, the appliance may be damaged) or above 40°C.
- Verify that the voltage of the electrical network corresponds to that indicated on the data plate of the device.
- In case of incompatibility between the power outlet and the appliance plug, have the power supply plug replaced with another suitable type.
- Place the appliance on a work surface away from water taps and sinks and heat sources.
- After removing the packaging, ensure the integrity of the appliance before its installation.
- Do not leave the materials used to package the machine within the reach of children.

## 5.2 Main wiring:

For proper operation, make the following connections:

- Power supply: Connect the power cable to the connector on the back of the device. Check that the connector is fully inserted before starting the system.

# 6 Cleaning the appliance

- It is mandatory to disconnect the plug from the electrical system when cleaning.
- Allow the appliance to cool before cleaning to avoid burns.
- Remove the coffee and capsule tank.
- Clean the body and accessories with a damp cloth and dry afterwards with a dry, non-abrasive cloth. The use of detergents is not recommended.
- Do not subject the appliance to heavy water jets or partial or total immersion.
- It is recommended to wash the tank and its lid daily and fill it with fresh drinking water.
- It is recommended to clean other parts that are in direct contact with food or that may come into contact with wastewater, at least once a week.

# 7 Criticality and Fault Management

## 7.1 In the event of failure of the appliance

Do not use the appliance in case the cable or plug is damaged, after a malfunction of the machine or after damage of any nature. Take the appliance to the nearest authorized service center for a check, repair, or verification that it is working properly. If the power cord is damaged, it must be changed by the manufacturer or their service. In case of failure or malfunction of the appliance, turn it off and do not tamper with it.

For any repairs, contact only a Technical Assistance Center authorized by the manufacturer and request the use of original spare parts. Failure to comply with the above may compromise the safety of the appliance and cause you to lose your right to the warranty.

CAUTION: KEEP THESE INSTRUCTIONS

## 7.2 Improper use of the appliance

The manufacturer cannot be considered liable for any damages resulting from improper, erroneous and unreasonable uses.

# 8. POWER SUPPLY

## 8.1 Instructions for the power cord

a) Extension cords may be used provided special care is taken during use.
b) If an extension cord is used:
1. Verify that the electrical power of the extension cord is at least equal to that of the device;
2. Place the longer cord so that it does not hang from the countertop or table to prevent children from pulling or tripping it.

The system uses a power system:

- External main power supply: 24V — 3A —72W.
- Backup power for data saving: 9V — 1.2Ah lithium manganese dioxide (Li-MnO₂ internal battery, which plays a non-critical role except for saving capsule data.

The battery must be housed in the appropriate compartment before switching on.

NOTE: Check the backup battery charge level regularly to ensure optimal system operation in the event of a main power failure.

# 9. SAFETY AND MAINTENANCE

## 9.1 Personal Protective Equipment (PPE)

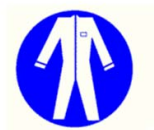
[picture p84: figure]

The following PPE must be used during commissioning and maintenance operations:

- Work gloves: to prevent cuts or mechanical injuries during interaction with metal and moving parts.
- Protective clothing: Clothes or aprons that do not limit movement, are resistant to cuts and do not allow entanglement.

If there is a need to handle the damaged Li-MnO2 9V stack, it is also mandatory to use the following PPE:

- Protective goggles: To prevent injury and irritation.
- Respiratory PPE: Masks or respirators with appropriate filters, as damaged batteries can release harmful gases or irritating dust during handling.
- Protective clothing: Clothes or aprons that do not limit movement and are resistant to acids/chemicals to protect skin and clothing from contamination.
- Operational safety notes:
1. Make sure the machinery is turned off and disconnected from the mains before each operation
2. It is highly recommended to remove the pile by at least 2.5 - 5 meters from combustible substances or components to limit the spread of a possible fire started by the damaged pile.
3. Avoid interventions in closed and poorly ventilated places to avoid inhaling harmful and irritating fumes.

NOTE: In case of malfunctions that cannot be resolved by the user, immediately stop the operation and contact the technical support service before proceeding with any other action on the machinery.

## 9.2 Safety Precautions

- Keep small parts out of the reach of children (risk of suffocation).
- Turn off and disconnect the power supply when the system is not in use, to prevent overheating and electrical hazards.
- Do not use the device in humid or wet environments.
- Use the required Personal Protective Equipment (PPE)

## 9.3 Periodic Maintenance

ACTIVITY | DESCRIPTION
Cleaning | Remove dust residue with a microfiber cloth. For deeper cleaning, you can rinse non-electronic parts with water.
Inspection | Periodically check the condition of the electrical cables and the absence of obstacles in the moving parts, coffee powder residues and/or stuck plastics.

## 9.4 Maintenance via diagnostics page on the user interface

To help the maintainer identify problems, it is possible to obtain elevated privileges through a login and consequently access the diagnostic page consisting of the event register (Log) of the machinery and the manual movement (Jog) of the stepper motors of the rotating drum and the punch.

How to access it:

Step 1: Locate the gear icon indicated in the figure on the main page:

Step 2: Enter the unique password provided to specialized maintainers:

Pic.3.1 Settings button

Pic. 3.2 Password diagnostic

## 9.5 Access the logger page to view diagnostic messages.

Pic 4.1

Pic 4.2 Logger Page (Clean with soap, refresh with air)

“Refresh” = reloads the list with the most recent messages

“Clean” = clears the entire diagnostic message list

## 9.6 Access the Jogger page for manual movement of the motors.

Pic 5.1 (Jogger access)

Step 1: Once you've entered the diagnostics page, you can only access the Jogger page if you haven't previously started the automatic process. You'll need to wait for it to finish or be put in STOP mode before accessing it. See (Pic. 5.2)

Pic 5.2 (Jogger access denied with machine in operation)

Step 2: Once you log in to the page, you will see the interface shown in the photo (Pic. 6.1).

Pic 6.1 (Jogger initial interface)

Enabling Motors: The motors must be enabled with the “ENABLE” button (Pic. 63.2) in order to be controlled.

Homing unavailable

Pic 6.2 (Enable motors)

Homing available

Fig. 6.3 (both motors enabled; from here you can Jog- and Jog+, or perform Homing)

Motor Configuration: Before performing a movement via Jog- or Jog+, you must set the "Degrees per click," or the motor's movement each time the Jog- or Jog+ button is pressed, and the desired "Speed." The maximum motor speed is 900°/s, and the punch travel from Min. to Max. Limit Switch is approximately 30 mm linear, or approximately 15 revolutions (5400°). Make sure that the punch does not collide with the drum (slewing ring) during movement.

The minimum and maximum configuration data are shown in the following table:

Value | Degrees per Click Drum | Speed [degrees/s] Drum | Degrees per Click Punch | Speed [degrees/s] Punch
Min | 1.8° | 0.0°/s | 1.8° | 0.0°/s
Max | [(9.22337E+18) - 1]° | 900°/s | 5400° | 900°/s

NOTE: The configuration data does not affect the homing speeds.

NOTE: The settings do not take into account reductions. A reduction of 1/3 should be considered for the drum (fifth wheel) (e.g., 3 motor revolutions = 1 drum revolution) and 2 mm linear per revolution (360°) for the punch (e.g., 5 motor revolutions = 10 mm punch). Click on the box where you want to change the value.

Press the text box to be able to change via the numeric keypad

Pic 6.4 (Selecting movement and speed parameters)

Movement with the Jog- and Jog+ buttons: The Jog- button (Pic 6.5) will move the motor counterclockwise, with the end of the shaft facing you. Jog+ (Pic 6.6) will move the motor clockwise.

NOTE: During any movement, the LEDs next to the word "Moving" will light up green. If the motor is stopped, they will remain red.

NOTE: Pressing Jog- and Jog+ repeatedly accumulates the movements, up to a maximum of 5.

Pic 6.5 (Jog- button pressed, counterclockwise movement)

Pic 6.6 (Jog+ button pressed, clockwise movement)

Homing: Initially, or whenever you need to move the motors to a specific position, it is recommended to perform homing by bringing the motors to their initial position to avoid damaging the machine. To do this, enable both motors (otherwise homing will not be permitted) as shown in the figure (Pic. 6.6), then press the "Homing" button shown in the figure (Pic. 6.3) and the motors will move at a preset speed to perform this action.

NOTE: To abort homing, you will need to press the "Homing" button again.

NOTE: During homing, you will not be able to press the "Jog-", "Jog+", or "Disable" buttons, nor will you be able to set the "Degrees per click" or "Speed [degrees/s]" for either motor. However, the sensor status will still be visible during all motor movements.

NOTE: During homing, the LEDs next to the word "Moving" will light up green. If the motor is stopped, they will remain red.

Pic 6.7 (Homing with flashing yellow-orange button)

## 9.6 Accessing the WiFi settings page

Pic 7.1 Accessing Wi-Fi settings

Pic. 7.2 WiFi Settings Screen

WiFi Connection: To connect to the WiFi connection, click the Network Name and Password boxes and use the keyboard at the bottom to enter the network name and password (pic. 7.2).

# 10. EMERGENCY MANAGEMENT

In case of blockage or anomaly:

- Immediate Stop: Stop all movement commands when opening the panel, make sure the fuses are not left in the fuse holder;
- Power Off: Turn off general power;
- Analysis: Identify the obstacle or mechanical failure before restarting.

# 11. MAINTENANCE LOG

Component | Intervention Type | Frequency | Method
Tub Organic Residues | Emptying and washing | Every 10 cycles | Neutral soap and water
Positioning Drum | Crusted Dust Removal | Bristle | Brush or Compressed Air
Punch and Scraper | Check plastic residue | Monthly | Microfiber wet cloth
Fan Cooling | Control dust obstruction | Monthly | External suction

# 12. DISPOSAL

At the end of the product's useful life, follow the disposal instructions below in compliance with current environmental regulations.

## 12.1 Dismantling procedure

- Remove the backup battery from its housing before any other operation.
- Identify reusable or recoverable components: motors, circuit boards, structural profiles, sensors, power supply.

## 12.2 Recycling of materials

MATERIAL | DESTINATION
Plastic / Aluminum | Separate collection according to local regulations.
Electronic Components (RAEE) | Confer at authorized disposal centers for electronic waste (RAEE).
Battery Li-MnO₂ | Special disposal at the point of collection of spent batteries (not in municipal waste).

23/06/26 REV.00.2 Pag.

23/006/26 REV.00.2 Pag.

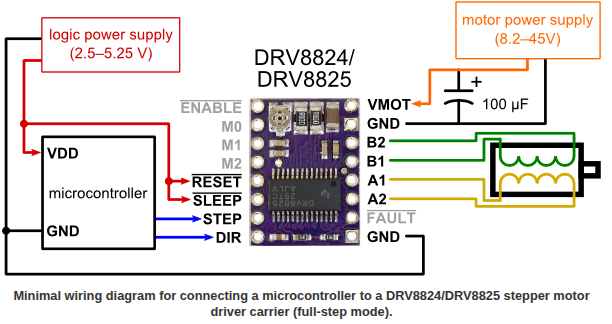
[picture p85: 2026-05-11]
Hardware/Datasheets/Motori/DRV8825/DRV8825_Pinout_&_Wiring.png

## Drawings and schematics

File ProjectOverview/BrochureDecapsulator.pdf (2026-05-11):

# DECAPSULATOR

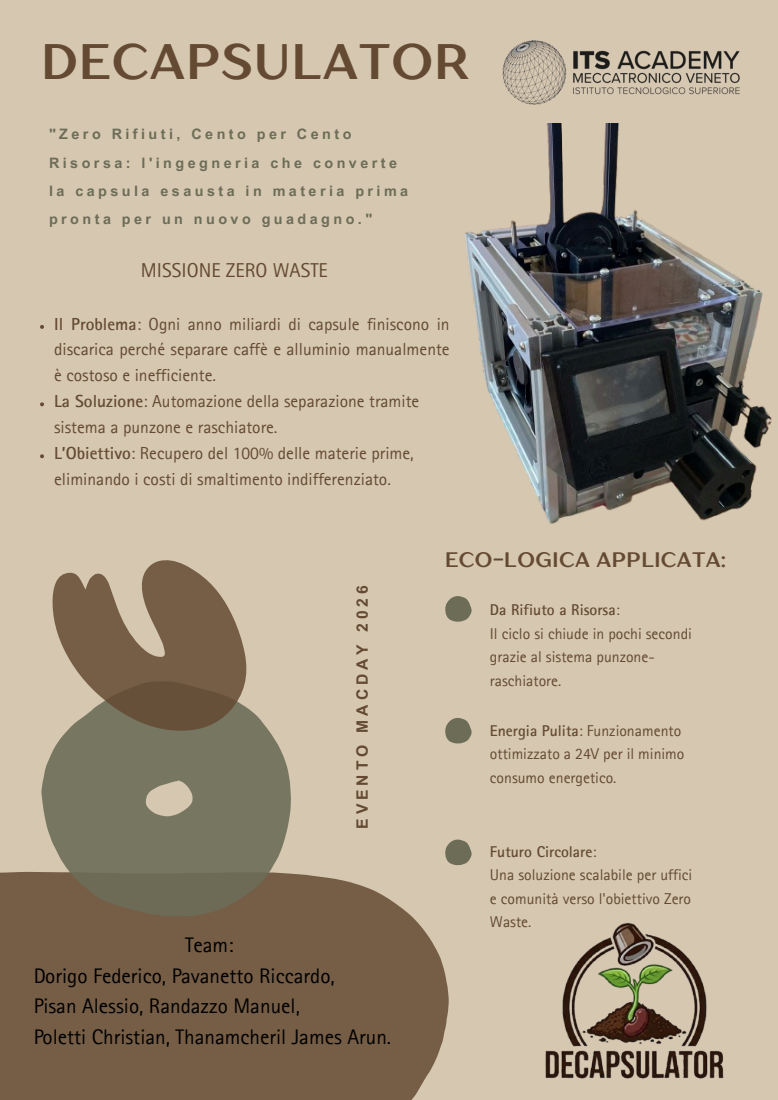
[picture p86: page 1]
Team:

MISSIONE ZERO WASTE

Il Problema: Ogni anno miliardi di capsule finiscono in
discarica perché separare caffè e alluminio manualmente
è costoso e inefficiente.
La Soluzione: Automazione della separazione tramite
sistema a punzone e raschiatore.
L’Obiettivo: Recupero del 100% delle materie prime,
eliminando i costi di smaltimento indifferenziato.

ECO-LOGICA APPLICATA:

Da Rifiuto a Risorsa:
Il ciclo si chiude in pochi secondi
grazie al sistema punzone-
raschiatore.

Energia Pulita: Funzionamento
ottimizzato a 24V per il minimo
consumo energetico.

Futuro Circolare:
Una soluzione scalabile per uffici
e comunità verso l'obiettivo Zero
Waste.

Dorigo Federico, Pavanetto Riccardo,
Pisan Alessio, Randazzo Manuel,
Poletti Christian, Thanamcheril James Arun.

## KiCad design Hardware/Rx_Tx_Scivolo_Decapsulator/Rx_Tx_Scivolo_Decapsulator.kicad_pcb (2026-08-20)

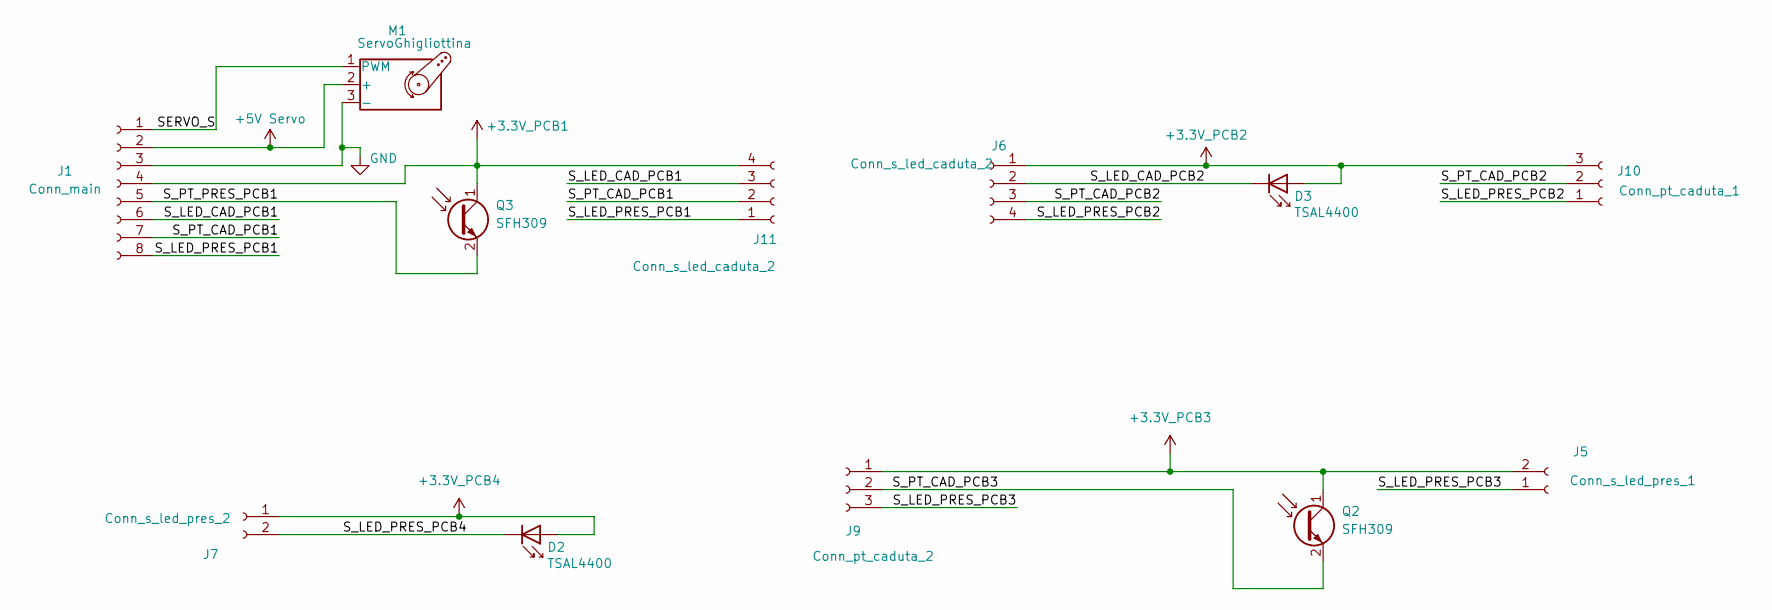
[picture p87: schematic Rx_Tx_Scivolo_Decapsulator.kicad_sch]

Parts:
D2, D3: TSAL4400; LED_D3.0mm_Clear
J1: Conn_main; JST_PH_S8B-PH-SM4-TB_1x08-1MP_P2.00mm_Horizontal
J5: Conn_s_led_pres_1; JST_PH_S2B-PH-SM4-TB_1x02-1MP_P2.00mm_Horizontal
J6, J11: Conn_s_led_caduta_2; JST_PH_S4B-PH-SM4-TB_1x04-1MP_P2.00mm_Horizontal
J7: Conn_s_led_pres_2; JST_PH_S2B-PH-SM4-TB_1x02-1MP_P2.00mm_Horizontal
J9: Conn_pt_caduta_2; JST_PH_S3B-PH-SM4-TB_1x03-1MP_P2.00mm_Horizontal
J10: Conn_pt_caduta_1; JST_PH_S3B-PH-SM4-TB_1x03-1MP_P2.00mm_Horizontal
M1: ServoGhigliottina; PinHeader_1x03_P2.54mm_Vertical_SMD_Pin1Right
Q2, Q3: SFH309; LED_D3.0mm_IRBlack

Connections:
+3.3V_PCB1: J1.4, J11.4, Q3.1 (C)
+3.3V_PCB2: D3.2 (A), J6.1, J10.3
+3.3V_PCB3: J5.2, J9.1, Q2.1 (C)
+3.3V_PCB4: D2.2 (A), J7.1
+5V Servo: J1.2, M1.2 (+)
/SERVO_S: J1.1, M1.1 (PWM)
/S_LED_CAD_PCB1: J1.6, J11.3
/S_LED_CAD_PCB2: D3.1 (K), J6.2
/S_LED_PRES_PCB1: J1.8, J11.1
/S_LED_PRES_PCB2: J6.4, J10.1
/S_LED_PRES_PCB3: J5.1, J9.3
/S_LED_PRES_PCB4: D2.1 (K), J7.2
/S_PT_CAD_PCB1: J1.7, J11.2
/S_PT_CAD_PCB2: J6.3, J10.2
/S_PT_CAD_PCB3: J9.2, Q2.2 (E)
/S_PT_PRES_PCB1: J1.5, Q3.2 (E)
GND: J1.3, J1.MP, M1.3 (-)

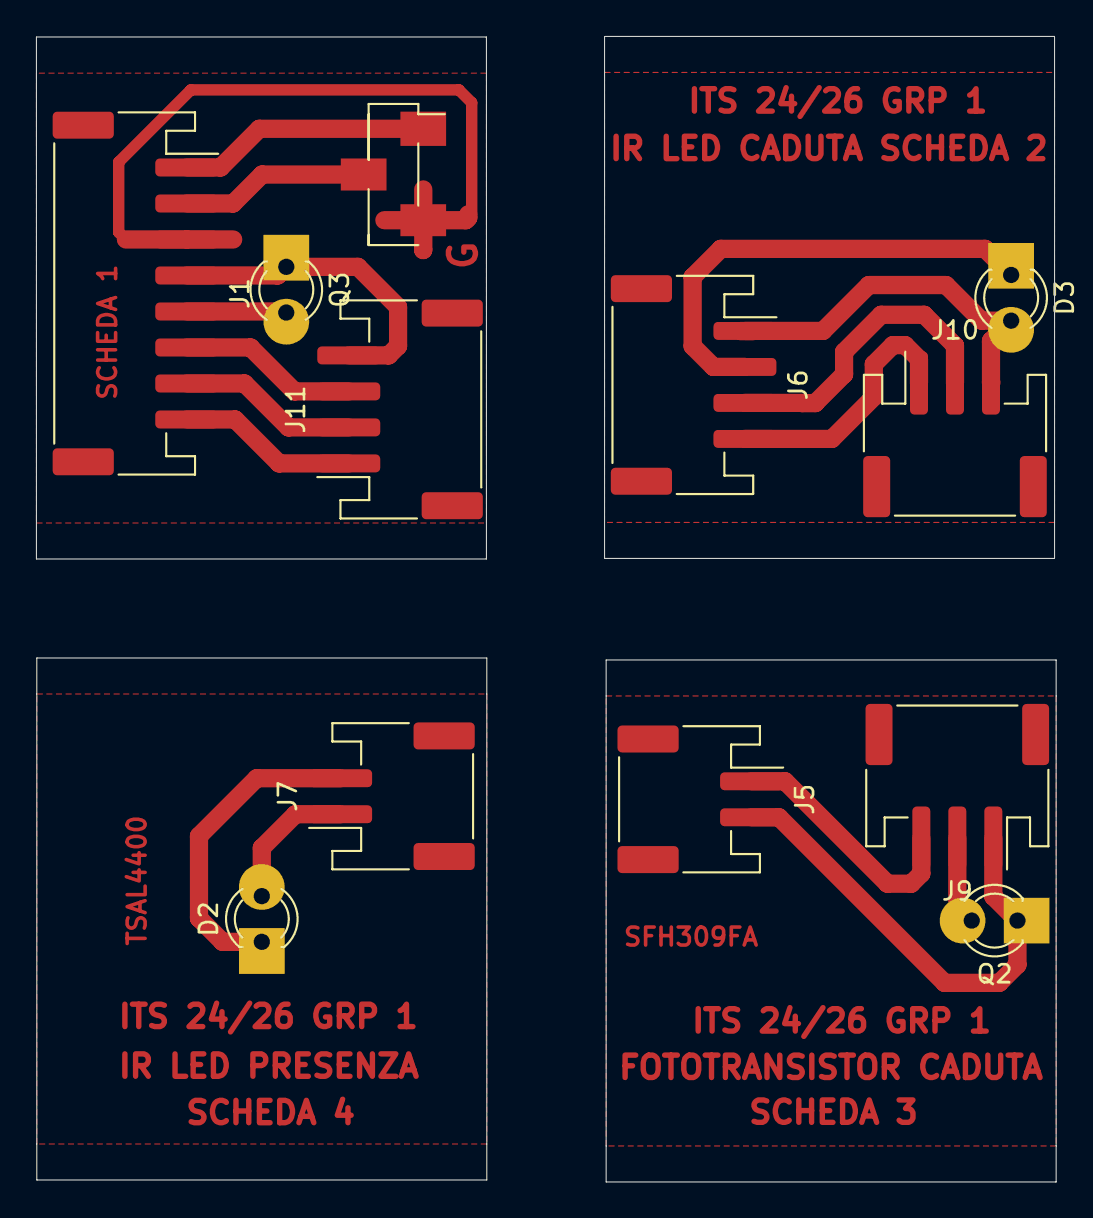
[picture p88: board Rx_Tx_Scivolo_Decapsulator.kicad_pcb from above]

Board: 2 copper layers, 56.7 x 63.6 mm, 12 parts (0 on the bottom side), 17 nets.

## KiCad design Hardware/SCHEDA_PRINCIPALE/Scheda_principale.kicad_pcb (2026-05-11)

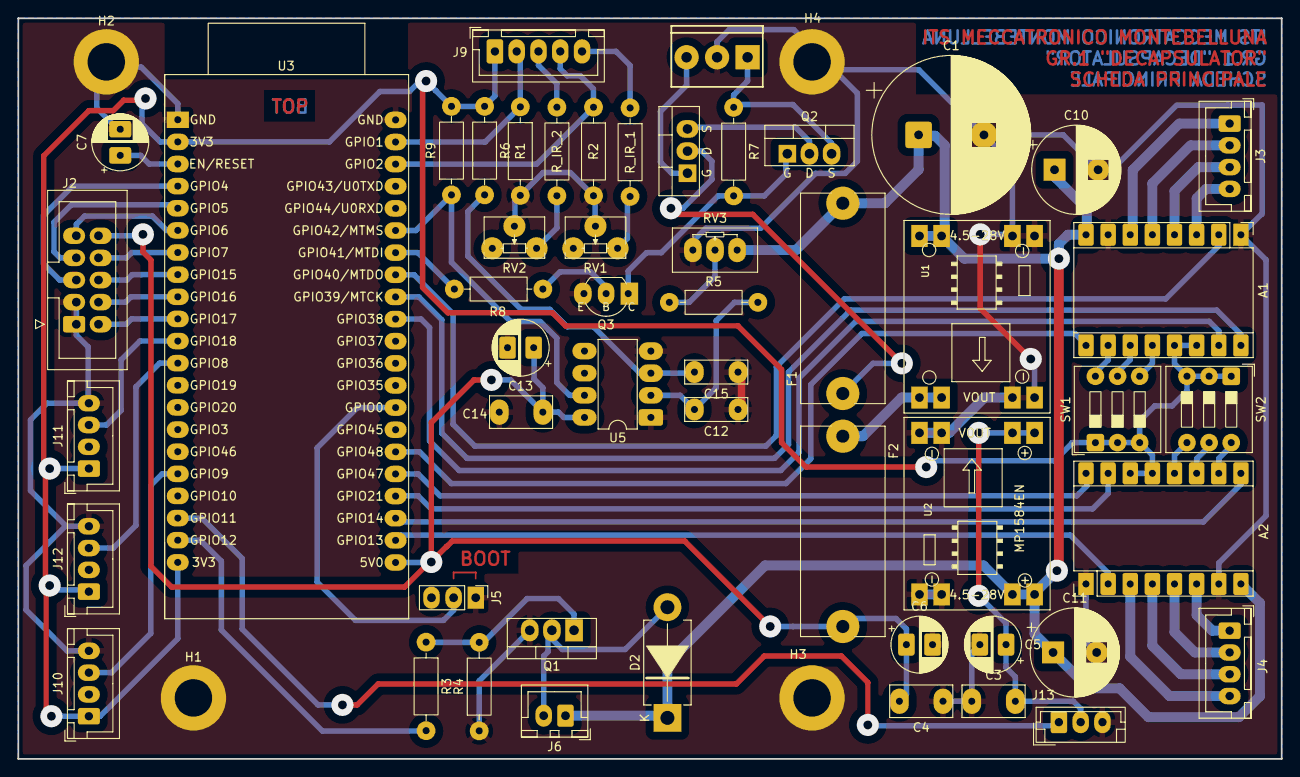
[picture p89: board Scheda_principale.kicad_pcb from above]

Board: 2 copper layers, 145.0 x 85.0 mm, 56 parts (0 on the bottom side), 61 nets.

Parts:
A1: Driver_motore_ralla; DRV8825
A2: Driver_motore_Punz; DRV8825
C1: 4700uF; CP_Radial_D18.0mm_P7.50mm
C3, C4: 330nF; C_Rect_L7.0mm_W3.5mm_P5.00mm
C5, C6, C13: 47uF; CP_Radial_D6.3mm_P2.50mm
C7: 10uF; CP_Radial_D6.3mm_P2.50mm
C10, C11: 470uF 35V; CP_Radial_D10.0mm_P5.00mm
C12, C15: 22nF; C_Rect_L7.0mm_W2.5mm_P5.00mm
C14: 100nF; C_Rect_L7.0mm_W3.5mm_P5.00mm
D1: SDT10A100CT; TO-220-3_Vertical_GDS
D2: 1N5822; D_DO-201AD_P12.70mm_Horizontal
F1, F2: Fuse; FUSE_4527
H1, H2, H3, H4: MountingHole_Pad; MountingHole_4.3mm_M4_DIN965_Pad
J1: Screw_Terminal_01x03; ScrewTerminal_1x03_P3.5mm_Blue
J2: Conn HMI; IDC-Header_2x05_P2.54mm_Vertical
J3: Conn_Mot_Ralla; JST_XH_B4B-XH-A_1x04_P2.50mm_Vertical
J4: Conn_Mot_Punz; JST_XH_B4B-XH-A_1x04_P2.50mm_Vertical
J5: Conn_BT_MCU; PinHeader_1x03_P2.54mm_Vertical
J6: Conn_Vent1; JST_XH_B2B-XH-A_1x02_P2.50mm_Vertical
J9: Conn_Phototrans; JST_XH_B5B-XH-A_1x05_P2.50mm_Vertical
J10: Conn_hall1; JST_XH_B4B-XH-A_1x04_P2.50mm_Vertical
J11: Conn_hall2; JST_XH_B4B-XH-A_1x04_P2.50mm_Vertical
J12: Conn_hall3; JST_XH_B4B-XH-A_1x04_P2.50mm_Vertical
J13: Conn_Servo; JST_EH_B3B-EH-A_1x03_P2.50mm_Vertical
Q1: IRLZ44N; TO-220-3_Vertical
Q2: IRF9540N; TO-220-3_Vertical_GDS
Q3: BC547B
R1, R2: 47k; R_Axial_DIN0207_L6.3mm_D2.5mm_P10.16mm_Horizontal
R3: 220; R_Axial_DIN0207_L6.3mm_D2.5mm_P10.16mm_Horizontal
R4: 10k; R_Axial_DIN0207_L6.3mm_D2.5mm_P10.16mm_Horizontal
R5, R6: 47K; R_Axial_DIN0207_L6.3mm_D2.5mm_P10.16mm_Horizontal
R7: 15k; R_Axial_DIN0207_L6.3mm_D2.5mm_P10.16mm_Horizontal
R8: 33k; R_Axial_DIN0207_L6.3mm_D2.5mm_P10.16mm_Horizontal
R9: 100k; R_Axial_DIN0207_L6.3mm_D2.5mm_P10.16mm_Horizontal
RV1, RV2: R_Potentiometer; Potentiometer_Bourns_3266W_Vertical
RV3: R_Potentiometer; Potentiometer_Bourns_3296W_Vertical
R_IR_1, R_IR_2: 27R - 1/4W; R_Axial_DIN0207_L6.3mm_D2.5mm_P10.16mm_Horizontal
SW1, SW2: SW_DIP_x03; SW_DIP_SPSTx03_Slide_9.78x9.8mm_W7.62mm_P2.54mm
U1, U2: MP1584
U3: ESP32-S3-DevKitC
U5: LM311; DIP-8_W7.62mm_LongPads

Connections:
+3V3: A1.13 (~RST), A1.14 (~SLP), A2.13 (~RST), A2.14 (~SLP), J9.1, J10.1, J11.1, J12.1, R6.1, R9.2, SW1.1, SW1.2, SW1.3, SW2.1, SW2.2, SW2.3, U3.3V3
+5V: C4.2, C6.1, C13.1, C14.2, F2.2, J2.10, U3.5V, U5.8 (V+)
+5V_SERVO: C3.2, C5.1, J13.2, U2.7 (VOUT1+), U2.8 (VOUT2+)
+9V: D1.3 (A1), Q2.2 (D)
+24V: A1.8 (VMOT), A2.8 (VMOT), C1.1, C10.1, C11.1, D2.1 (K), F1.2, J6.1, RV3.1, U1.3 (VIN1+), U1.4 (VIN2+), U2.3 (VIN1+), U2.4 (VIN2+)
/Project Architecture/Section A - Scheda Principale/Interface A - Interconnects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: J11.3, U3.18 (GPIO18/ADC2_CH7)
/Project Architecture/Section A - Scheda Principale/Interface A - Interconnects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: J12.3, U3.8 (GPIO8/ADC1_CH7)
/Project Architecture/Section A - Scheda Principale/Interface A - Interconnects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: J10.3, U3.9 (GPIO9/ADC1_CH8)
/Project Architecture/Section A - Scheda Principale/Interface A - Interconnects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: J2.2, U3.17 (GPIO17/ADC2_CH6)
/Project Architecture/Section A - Scheda Principale/Interface A - Interconnects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: J2.8, U3.7 (GPIO7/ADC1_CH6)
/Project Architecture/Section A - Scheda Principale/Interface A - Interconnects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: J2.9, U3.6 (GPIO6/ADC1_CH5)
/Project Architecture/Section A - Scheda Principale/Interface A - Interconnects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: J2.6, U3.15 (GPIO15/ADC2_CH4/32K_P)
/Project Architecture/Section A - Scheda Principale/Interface A - Interconnects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: J2.4, U3.16 (GPIO16/ADC2_CH5/32K_N)
/Project Architecture/Section A - Scheda Principale/Interface A - Interconnects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: J2.7, U3.5 (GPIO5/ADC1_CH4)
/Project Architecture/Section A - Scheda Principale/Interface A - Interconnects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: J2.5, U3.4 (GPIO4/ADC1_CH3)
/Project Architecture/Section A - Scheda Principale/Interface A - Interconnects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: A2.4 (A1), J4.3
/Project Architecture/Section A - Scheda Principale/Interface A - Interconnects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: A2.3 (A2), J4.4
/Project Architecture/Section A - Scheda Principale/Interface A - Interconnects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: A2.5 (B1), J4.2
/Project Architecture/Section A - Scheda Principale/Interface A - Interconnects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: A2.6 (B2), J4.1
/Project Architecture/Section A - Scheda Principale/Interface A - Interconnects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: J13.1, U3.11 (GPIO11/ADC2_CH0)
/Project Architecture/Section A - Scheda Principale/Interface A - Interconnects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: A1.4 (A1), J3.3
/Project Architecture/Section A - Scheda Principale/Interface A - Interconnects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: A1.3 (A2), J3.4
/Project Architecture/Section A - Scheda Principale/Interface A - Interconnects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: A1.5 (B1), J3.2
/Project Architecture/Section A - Scheda Principale/Interface A - Interconnects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: A1.6 (B2), J3.1
/Project Architecture/Section A - Scheda Principale/Interface A - Interconnects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: J9.3, R_IR_2.1
/Project Architecture/Section A - Scheda Principale/Interface A - Interconnects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: J9.5, R_IR_1.1
/Project Architecture/Section A - Scheda Principale/Interface A - Interconnects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: J9.4, R2.1, U3.2 (GPIO2/ADC1_CH1)
/Project Architecture/Section A - Scheda Principale/Interface A - Interconnects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: J9.2, R1.1, U3.1 (GPIO1/ADC1_CH0)
/Project Architecture/Section A - Scheda Principale/MCU/AK_DO: R9.1, U3.42 (GPIO42/MTMS), U5.7
/Project Architecture/Section A - Scheda Principale/MCU/AK_INT: R8.2, U3.41 (GPIO41/MTDI)
/Project Architecture/Section A - Scheda Principale/MCU/BOOT_MCU: J5.2, U3.0 (GPIO0)
/Project Architecture/Section A - Scheda Principale/MCU/CONTR_VENT: R3.2, U3.12 (GPIO12/ADC2_CH1)
/Project Architecture/Section A - Scheda Principale/MCU/PUNZ_DIRECTION_DRV: A2.16 (DIR), U3.47 (GPIO47)
/Project Architecture/Section A - Scheda Principale/MCU/PUNZ_ENABLE_DRV: A2.9 (~EN), U3.14 (GPIO14/ADC2_CH3)
/Project Architecture/Section A - Scheda Principale/MCU/PUNZ_FAULT: A2.2 (~FLT), U3.13 (GPIO13/ADC2_CH2)
/Project Architecture/Section A - Scheda Principale/MCU/PUNZ_STEP_DRV: A2.15 (STEP), U3.21 (GPIO21)
/Project Architecture/Section A - Scheda Principale/MCU/RALLA_DIRECTION_DRV: A1.16 (DIR), U3.39 (GPIO39/MTCK)
/Project Architecture/Section A - Scheda Principale/MCU/RALLA_ENABLE_DRV: A1.9 (~EN), U3.48 (GPIO48)
/Project Architecture/Section A - Scheda Principale/MCU/RALLA_FAULT: A1.2 (~FLT), U3.40 (GPIO40/MTDO)
/Project Architecture/Section A - Scheda Principale/MCU/RALLA_STEP_DRV: A1.15 (STEP), U3.38 (GPIO38)
/Project Architecture/Section A - Scheda Principale/Misc - Autokill/VBAT: J1.1, Q2.3 (S), R7.1
GND: A1.1 (GND), A1.7 (GND), A2.1 (GND), A2.7 (GND), C1.2, C3.1, C4.1, C5.2, C6.2, C7.2, C10.2, C11.2, C12.1, C13.2, C14.1, C15.1, H1.1, H2.1, H3.1, H4.1, J1.2, J2.1, J2.3, J5.1, J10.4, J11.4, J12.4, J13.3, Q1.3 (S), Q3.3 (E), R1.2, R2.2, R4.1, RV1.2, RV2.2, RV3.3, U1.1 (VIN1-), U1.2 (VIN2-), U1.5 (VOUT1-), U1.6 (VOUT2-), U2.1 (VIN1-), U2.2 (VIN2-), U2.5 (VOUT1-), U2.6 (VOUT2-), U3.G (GND), U5.1 (GND), U5.4 (V-)
unnamed: A1.10 (M0), SW1.6
unnamed: A1.11 (M1), SW1.5
unnamed: A1.12 (M2), SW1.4
unnamed: A2.10 (M0), SW2.6
unnamed: A2.11 (M1), SW2.5
unnamed: A2.12 (M2), SW2.4
unnamed: D1.1 (A2), J1.3
unnamed: D1.2 (K), F1.1
unnamed: D2.2 (A), J6.2, Q1.2 (D)
unnamed: Q1.1 (G), R3.1, R4.2
unnamed: Q2.1 (G), Q3.1 (C), R7.2
unnamed: Q3.2 (B), R8.1
unnamed: R5.1, RV3.2
unnamed: RV1.3, R_IR_1.2
unnamed: RV2.3, R_IR_2.2
unnamed: F2.1, U1.7 (VOUT1+), U1.8 (VOUT2+)
unnamed: C7.1, U3.RST (CHIP_PU)
unnamed: C12.2, R5.2, U5.2 (+)
unnamed: C15.2, R6.2, U5.3 (-)

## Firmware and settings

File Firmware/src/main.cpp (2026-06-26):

// -*- Gruppo 1-FreeRTOS-C++

/**
 * This file is part of {{ Decapsulator }}.
 *
 * Developed for the ITS Meccatronico Montebelluna-Castelfranco Veneto 2024-2026 Gruppo 1.
 * This product includes software developed by the Gruppo 1 Project.
 * See the COPYRIGHT file at the top-level directory of this distribution
 * for details of code ownership.
 *
 * This program is NOT free software: you can NOT redistribute it and/or modify it.
 *
 * The Documentation is made following the Doxygen standard documentation style
 *
 *
 * About Code and Libraries stable versions compatibility and Libraries Documentation:
 *
 * @c_plus_plus_reference_documentation_link: https://learn.microsoft.com/it-it/cpp/cpp/?view=msvc-170
 *
 * @freertos_reference_documentation: https://www.freertos.org/Documentation/00-Overview
 */

#include "Arduino.h" // Per il supporto da altri IDE (Integrated Development Environment)
#include "Tasks.hpp"
#include "tasks_cfg.hpp"
#include "decapsulator_io.hpp"
#include "Debug.hpp"
#include "OverTheAir_OTA.hpp"
#include "DecapsulatorPRG.hpp"
#include "JogMotoriPRG.hpp"
#include "HMI.hpp"
#include "AutoKillPRG.hpp"
#include "DateAndTimePRG.hpp"
#include "HMI_UI_EEZ/created_post_prj_export/ui_vars_mutexs.h"

/**
 *  @brief il setupTask() crea le task e ritorna i log in caso di errore per tutte le task non create con successo 
 *
 *  @param void
 *
 *  @return pdPASS se è andata a buon fine - pdFAIL se c'è stato un errore
 */
BaseType_t setupTasks(void)
{
    BaseType_t status = pdPASS;

    /// Creazione della task di LOGGER
    status &= xTaskCreatePinnedToCore(LoggerTask, "task LOGGER", Logger_heap, NULL, Logger_priority, &LoggerHandler, APP_CPU_NUM);

    /// Inizializzazione degli IO del decapsulator
    status &= decapsulator_io_begin();

    /// Inizializzazione dei mutex delle variabili utilizzate tra Frontend & Backend
    status &= ui_init_var_mutexs() ? pdPASS : pdFAIL;

    /// Creazione della task della Human Machine Interface
    status &= xTaskCreatePinnedToCore(prgHMITask, "task HMI PRG", HMI_heap, NULL, HMI_priority, &HMIPrgHandler, APP_CPU_NUM); 

    /// Creazione della task per il download del firmware
    //status &= OverTheAir.Init("task OTA", OTA_heap, NULL, OTA_priority, OTA_delay, OTA_Setup, OTA_Loop);

    /// Creazione della task di gestione del programma principale
    status &= xTaskCreatePinnedToCore(prgDecapsulatorTask, "task MAIN PRG", MainPrg_heap, NULL, MainPrg_priority, &MainPrgHandler, APP_CPU_NUM);

    /// Creazione della task per il controllo manuale dei motori
    status &= xTaskCreatePinnedToCore(prgJogMotoriTask, "task JOG MOTORI", JogMotori_heap, NULL, JogMotori_priority, &JogMotoriPrgHandler, APP_CPU_NUM);

    /// Creazione della task per la gestione dell'autokill e del salvataggio dei dato in microSD
    status &= xTaskCreatePinnedToCore(AutoKillTask, "task AUTOKILL", Autokill_heap, NULL, Autokill_priority, &AutokillHandler, APP_CPU_NUM);

    /// Creazione della task per la gestione della data e ora tramite RTC e sincronizzazione NTP
    status &= xTaskCreatePinnedToCore(DateAndTimePRG, "task update RTC", DateAndTime_heap, NULL, DateAndTime_priority, &DateAndTimeHandler, APP_CPU_NUM);

    /// Restituisce lo stato generale di errore di almeno una delle task, comunque ci sono i log
    return status;
}

/**
 *  @brief Setup per la definizione delle task e inizializzazione dei componenti
 */
void setup()
{
    vTaskPrioritySet(NULL, configMAX_PRIORITIES-1);
    pinMode(RALLA_ENABLE_PIN, OUTPUT);
    digitalWrite(RALLA_ENABLE_PIN, HIGH); // Disabilita ralla
    pinMode(PUNZ_ENABLE_PIN, OUTPUT);
    digitalWrite(PUNZ_ENABLE_PIN, HIGH); // Disabilita punzone
    
    /// crea le task, superato il timeout restarta l'esp32
    const uint32_t tmoSetupTask = millis();
    while(!setupTasks())
    {
        if(millis() - tmoSetupTask >= 1000)
        {
            LogError("setup", "Impossibile creare le task nel tempo specificato");
            ESP.restart();
        }
    }

    LogInfo("setup", "create le tasks - Free Stack Space: %d", uxTaskGetStackHighWaterMark(NULL));

    vTaskPrioritySet(NULL, 0);
}

/**
 *  @brief loop principale
 *        
 *  @note Non serve perchè le tasks vengono gestite dallo scheduler
 *
 *  @attention Non eliminare la task perchè serve al WiFi
 * 
 */
void loop()
{
    
}

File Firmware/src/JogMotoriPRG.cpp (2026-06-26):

#include "JogMotoriPRG.hpp"
#include "HMI_UI_EEZ/created_post_prj_export/ui_vars_mutexs.h"
#include "HMI_UI_EEZ/vars.h"


void prgJogMotoriTask(void *pvParameters)
{
    TickType_t getLastTick = xTaskGetTickCount();

    /// Sequenza Homing
    uint8_t StateHoming = 0;

    double gradi_per_click_ralla = 360.0;
    double speed_motore_ralla    = 90.0;
    double gradi_per_click_punz  = 360.0;
    double speed_motore_punz     = 90.0;

    /// Si assicura di Auto-sospendersi per evitare problemi con le risorse condivise (motori)
    /// Sarà la task dell'HMI che deciderà se sospendere o attivare le task del programma main e di jog
    vTaskSuspend(NULL);

    uint32_t tmr = 0;
    
    while(1)
    {
        #pragma region (PUNZONE)

        /// Legge il sensore di finecorsa MINIMO del Punzone
        if(MotPunzone.HardMin.event())
            set_var_stato_finecorsa_min(MotPunzone.HardMin.rawRead() == (int8_t)(PUNZ_CAM_SIGNAL));

        /// Legge il sensore di finecorsa MASSIMO del Punzone
        if(MotPunzone.HardMax.event())
            set_var_stato_finecorsa_max(MotPunzone.HardMax.rawRead() == (int8_t)(PUNZ_CAM_SIGNAL));
        
        /// Converte le stringhe in numeri double positivi
        gradi_per_click_punz = abs(String(get_var_gradi_per_click_punz()).toDouble());
        speed_motore_punz    = abs(String(get_var_speed_motore_punz()).toDouble());

        /// Enable/Disable Motore Punzone
        if(get_var_comando_motore_punzone() == true)
        {
            if(MotPunzone.isDetached())
            {
                MotPunzone.attach();
                MotPunzone.Start();
            }
        }
        else
        {
            if(MotPunzone.isAttached())
            {
                MotPunzone.abortCurrentCommand();
                xQueueReset(queue_direzione_comando_punzone);
                MotPunzone.Stop(RELEASE);
                MotPunzone.detach();
            }
        }

        if(MotPunzone.isStepDone())
        {
            int8_t punz_jog_dir = 0;
            if(xQueueReceive(queue_direzione_comando_punzone, &punz_jog_dir, 0) == pdTRUE)
                MotPunzone.moveRel(punz_jog_dir * gradi_per_click_punz, speed_motore_punz);
        }

        
        set_var_stato_motore_punzone(StateHoming == 0 ? !MotPunzone.isStepDone() : !MotPunzone.isHomeDone());

        #pragma endregion (PUNZONE)
        




        
        
        #pragma region (RALLA)
        
        /// Converte le stringhe in numeri double positivi
        gradi_per_click_ralla = abs(String(get_var_gradi_per_click_ralla()).toDouble());
        speed_motore_ralla    = abs(String(get_var_speed_motore_ralla()).toDouble());

        /// Legge il sensore di calibrazione della RALLA
        set_var_stato_sensore_di_calibrazione(MotRalla.HardMax.rawRead() == (int8_t)(RALLA_CAM_SIGNAL));
                    
        /// Enable/Disable Motore Tamburo
        if(get_var_comando_motore_ralla() == true)
        {
            if(MotRalla.isDetached())
            {
                MotRalla.attach();
                MotRalla.Start();
            }
        }
        else
        {
            if(MotRalla.isAttached())
            {
                MotRalla.abortCurrentCommand();
                xQueueReset(queue_direzione_comando_ralla);
                MotRalla.Stop(RELEASE);
                MotRalla.detach();
            }
        }

        if(MotRalla.isStepDone())
        {
            int8_t ralla_jog_dir = 0;
            if(xQueueReceive(queue_direzione_comando_ralla, &ralla_jog_dir, 0) == pdTRUE)
                MotRalla.moveRel(ralla_jog_dir * gradi_per_click_ralla, speed_motore_ralla);
        }

        set_var_stato_motore_ralla(StateHoming == 0 ? !MotRalla.isStepDone() : !MotRalla.isHomeDone());
            
        #pragma endregion (RALLA)
        
        

        #pragma region (HOMING)

        /// Blocca l'homing se l'utente ripreme il tasto
        if(get_var_homing() == false && StateHoming != 0)
        {
            MotPunzone.abortCurrentCommand();
            MotRalla.abortCurrentCommand();
            MotRalla.removeHardLimits();
            StateHoming = 0;
        }

        switch(StateHoming)
        {
            case 0 : /// NO HOMING IN CORSO
            {
                if(get_var_homing() == true)                
                {
                    MotPunzone.abortCurrentCommand();
                    MotRalla.abortCurrentCommand();
                    MotRalla.removeHardLimits();
                    xQueueReset(queue_direzione_comando_punzone);
                    xQueueReset(queue_direzione_comando_ralla);
                    StateHoming++;
                }
            }
            break;

            case 1 : /// HOMING CMD PUNZONE
            {
                MotPunzone.home(PUNZ_HOME_SPEED, HARD_MAX, PUNZ_HOME_DIR, PUNZ_POST_HOME_POS);
                StateHoming++;
            }
            break;

            case 2 : /// HOMING WAIT DONE PUNZONE
            {
                if(MotPunzone.isHomeDone())
                {
                    MotRalla.reattachHardLimits();
                    StateHoming++;
                }
            }
            break;

            case 3 : /// HOMING CMD RALLA
            {
                int8_t RallaHardMaxStatus = MotRalla.HardMax.rawRead();
                
                if(RallaHardMaxStatus != -1)
                {
                    if(RallaHardMaxStatus == RALLA_CAM_SIGNAL)
                    {
                        if(MotRalla.isStepDone())
                            MotRalla.moveRel(-RALLA_HOME_DIR * 360.0 * GEAR_RATIO_RALLA, RALLA_HOME_CONT_SPEED);
                    }
                    else
                    {
                        double gradi_post_home = 0.0;
                        if(!MotRalla.isStepDone())
                        {
                            MotRalla.abortCurrentCommand();
                            gradi_post_home = -3.3 * GEAR_RATIO_RALLA;
                        }
                        else
                            gradi_post_home = RALLA_POST_HOME_POS * GEAR_RATIO_RALLA;

                        MotRalla.home(RALLA_HOME_SPEED, HARD_MAX, RALLA_HOME_DIR, gradi_post_home);
                        StateHoming++;
                    }
                }
            }
            break;

            case 4 : /// HOMING WAIT DONE RALLA
            {
                if(MotRalla.isHomeDone())
                {
                    MotRalla.removeHardLimits();
                    StateHoming = 0;
                    set_var_homing(false);
                    /// @todo notificare che bisogna skippare un'apertura del ServoParatia
                }
            }
            break;
        }

        #pragma endregion (HOMING)
                

        xTaskDelayUntil(&getLastTick, JogMotori_delay);
    }

    vTaskDelete(NULL);
}

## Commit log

2025-12-07 FIX: Minors bugs in Debug file and WiFi_secrets now called WiFi_Config
    [BaseFileTemplate_secrets.hpp, main.cpp]
2025-12-18 UPDATE: Salvataggio prima di cambiare radicalmente tutta la gestione delle task che avverrà su un altro branch
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2025-12-21 refactor(Motion Controller): aggiornata la gestione dovuto alla modifica della libreria del DRV8825
2025-12-21 style(debugger file): resa più visibile all'utente le funzioni e la configurazione del debbugger che può fare
2025-12-25 refactor(stepper driver): migliorata la gestione del DRV8825 per girare in una task già esistente
2025-12-25 refactor(debug): Aggiunto un timeout al take del semaforo della seriale per evitare corruzione di messaggi
2026-01-03 refactor(MotionControl): Portata ad un livello stabile la gestione del motion in quanto ora è capace di far effetivamente girare il motore :)
2026-01-03 refactor(Debug handle): Migliorata la gestione dell'acquisizione del semaforo per la seriale e l'mqtt con verifica di effettiva acquisizione del semaforo
2026-01-03 refactor(motion handling): Cambiato il controllo del motion e reso sia la classe MOTION che la classe DRV8825 stabili, ancora non provato l'Homing del MOTION
2026-01-03 fixed(Debug handle): Ora in caso si tolga il logger MQTT non vi saranno errori di compilazione dovuti all'ommisione del controllo della funzione 'DebugOverrideVar'
2026-01-04 test(refactored motion controller): testato la nuova versione del motion controller, commit fatto per un futuro in cui potrebbe servire un test rapido già fatto
2026-01-04 Revert "fixed(Debug handle): Ora in caso si tolga il logger MQTT non vi saranno errori di compilazione dovuti all'ommisione del controllo della funzione 'DebugOverrideVar'"
    This reverts commit 9834df87bfcddb4dfee4a810bb896123dcf9482b.
2026-01-04 Revert "fixed(Debug handle): Ora in caso si tolga il logger MQTT non vi saranno errori di compilazione dovuti all'ommisione del controllo della funzione 'DebugOverrideVar'"
    This reverts commit c21fe2894116f849319a74eca6f76d7c701a08a2.
2026-01-04 refactor(Debug handle): Ora in caso si tolga il logger MQTT non vi saranno errori di compilazione dovuti all'ommisione del controllo della funzione 'DebugOverrideVar', aggiunta anche la possibilità d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
2026-01-04 refactor(Task class debug handle): aggiunta la possibilità di disattivare i log della classe 'TaskTypeDef'
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2026-01-29 refactor(DRV8825 lib properties) modificate le proprietà della libreria come ad esempio l'autore e il repo git in cui trovarlo:
2026-01-29 organization(Motion Control): diviso la parte di sviluppo dei metodi dalla definizione della classe per leggibilità, spostato i file in lib/MotionControl
2026-01-29 add(helper debounce): aggiunto un helper per la gestione dei pin input interrupt e polling con debounce
2026-01-29 moved(MotionControl): spostata e riorganizzata la gestione del codice didicato al motion control
2026-03-07 Fix(Task.hpp linking issue after compilation): fixato il problema di linking dopo la compilazione, il problema era dato dal fatto che in c++ non si possono dichiarare funzioni/metodi nel file source(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
    [main.cpp]
2026-03-14 refactor(debounce pin handler): rivisitata a debuggata e testate la gestione sia del polling che dell'interrupt per i pin di input
2026-03-18 refactor(MotionControl): Aggiunta la gestione degli Hard Limits Max e Min, ancora da testare
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2026-03-19 refactor(DRV8825_Decapsulator lib): rimosso l'uso del DMA e fixato il problema degli RMT channel esauriti
2026-03-19 refactor(MotionControl): Testata e approvata la gestione degli Hard Limits Max e Min e dell'Homing(funzionante)
2026-03-19 fixed(Debounce Pin) : fixato tutti i return che non cedevano il semaforo con xSemaphoreGive
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2026-04-08 add(remove hardLimits): aggiunta la funzione removeHardLimits e migliorata la gestione degli hard limits durante l'homing
2026-04-08 add(getLevelTrigger) : aggiunta la funzione per ottenere dall'esterno la soglia di trigger impostata così che l'utente non debba memorizzare esternamente una variabile memorizzata interamente dalla c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
2026-04-08 remove (logs): rimossi dei log fatti direttamente con la seriale e non con i log del decapsulator
2026-04-08 add(timeout): aggiunto timeout di setup delle task che fa riavviare l'ESP32 se superato
2026-04-08 improved and renamed (prg main): rinominato e scisso in due file (cpp e hpp) separati, inserita la gestione delle code di comunicazione Frontend<-->Backend. Modificata tutta la sequenza del macchinar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
2026-04-11 reorganized (HMI): sistemato i file dell'HMI togliendo il file TFT_Display.hpp per questione di comprensione dei file
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2026-04-15 refactor(WiFi Start Option): resa disponibilità di non far inizializzare il WiFi, esce un warning all'upload (voluto da me) che dice che non sarà possibile usare il logger e caricare lo sketch da rem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
2026-04-15 reorganized: HMI ora ha la sua zona "isolata" per evitare il più possibile merge conflict
2026-04-16 reorganized(main): riorganizzato il main per avere un log di errore nel caso sia impossibile creare le task entro il timeout previsto
    [main.cpp]
2026-04-16 changed(WiFi timeout): aumentato il timeout di inizializzazione del WiFi da 4000ms a 5000ms
2026-04-16 DEPRECATED(removed(legacy variables) added(logs, task standard improvements)): a breve sarà rimossa la classe delle task per ridurre l'overhead e semplificare il codice. Tolte le vecchie variabili di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
2026-04-17 updated(Programma principale): è stato aggiornato il programma principale in base a i pin reali che verranno usati sul PCB. Testato anche il codice principale, non è ultimato ma almeno è un abbastanz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
2026-04-17 add(timeout rmt transmission): aggiunto un timeout di trasmissione dell'rmt di 10ms al posto di un wait infinito
2026-04-17 fix(back dir negativo): risolto il bug che non faceva andare avanti il motore nel caso fosse negativo il PostHomeVal
2026-04-17 add(Logger Task): è stata improntata una task per il logger nel caso si vogliano salvare i dati in SD e per intrdurre meno jitter quando si logga.
2026-04-17 add(HMI task config): aggiunte le variabili per la task HMI e cambiata la quantità di memoria allocata, la priorità e il delay delle altre task (OTA e MainPrg)
2026-04-17 Squashed commit of the following:
    commit 8ea9806c0ff006b2b9380404b9968e63bbac8379
    Author: Manuel Randazzo <randazzomanuel05@gmail.com>
    Date: Fri Apr 17 23:28:18 2026 +0200
    add(HMI task config): aggiunte le variabili per la task HMI e cambiata la quantità di memoria allocata, la priorità e il delay delle altre task (OTA e MainPrg)
    commit 42d5affd46dfeb5ffe7ee91fce9a7a2a139dfbec
    Author: Manuel Randazzo <randazzomanuel05@gmail.com>
    Date: Fri Apr 17 23:20:39 2026 +0200
    add(Logger Task): è stata improntata una task per il logger nel caso si vogliano salvare i dati in SD e per intrdurre meno jitter quando si logga.
    commit 758cfc662febe6b9723cbe984f2c446a398fc8d8
    Author: Manuel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
    [DecapsulatorPRG.cpp, main.cpp]
2026-04-18 refactor(WiFi wait connection with timeout) : Cambiato il vecchio approccio di verificare nello startup se si connetteva il WiFi con una API già inclusa nella classe WiFi che fa la stessa cosa
2026-04-28 stable(programma principale): reso stabile e funzionante il programma del Decapsulator, da ora in poi bisogna stare attenti a non rompere il funzionamento
2026-04-28 add(R_TRIG): aggiunta una classe che rileva qualora vi sia un rising edge di una variabile a livello software
2026-04-28 add(F_TRIG): aggiunta una classe che rileva qualora vi sia un falling edge di una variabile a livello software
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2026-05-13 fix(log funzioni tx e rx delle code) : non c'erano degli adeguati return nei log delle funzioni di checkUpdate e sendUpdate
    [DecapsulatorPRG.cpp]
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2026-05-22 add(accelerations) : aggiunta la creazione di un profilo di velocità trapezoidale con accelerazione costante. ToDo fare un profilo ad S con Jerk se ci sono problemi con l'accelerazione così impulsiva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
2026-05-22 add(template lv_conf) : è stato fatto un tamplate, questo file deve essere rinominato in "lv_conf.h" e messo nella directory ".pio->libdeps->esp32-s-devkitc1-n16r8->lvgl" altrimenti darà errori di co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
2026-05-23 move and fix(ui generated files) : sono stati spostati i file generati da SquareLine in "src/HMI_UI" del progetto per non causare problemi con il programma e non generare errori di dipendenze
2026-05-24 fix(TFT Config) : aggiunto il pin SD, invertiti il MISO e il MOSI per un errore sulla scheda principale, rimosse tante righe inutili come dimensioni display e directory "lib/*", rimosse tutte le buil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
2026-05-25 fix(include path lv_conf.h) : risolto il problema di lv_conf.h che prima non riuscivamo a mettere nel path /include/ del progetto. E' stata scelta l'opzione di non usare direttamente il path del prog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
2026-05-25 fix(include path lv_conf.h) : risolto il problema di lv_conf.h che prima non riuscivamo a mettere nel path /include/ del progetto. E' stata scelta l'opzione di non usare direttamente il path del prog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
2026-06-03 add(to prj path lib, .cpp, base object "SaveToFIle SD") : aggiunto il file SavingFilesSD.cpp e aggiunta la classe alle librerie del progetto. Fixate dei metodi che in compilazione non venivano visti 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
2026-06-03 update(Debugger) : passati da una gestione inline ad una gestione attraverso una coda la quale comunica ad una task dedicata il messaggio da loggare. Fixato il problema della comunicazione MQTT per i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
2026-06-04 fix(LOGS Motion Controller) : risolti alcuni problemi con il logger del Motion Controller
2026-06-04 fix(begin fan pin) : risolto il problema per il quale la ventola non veniva inizializzata. Il motivo era che veniva passato fan_pin e non pin alla funzione pinMode nel begin.
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2026-06-05 add(External SPI) : aggiunta la possibilità di passare un'istanza SPI (per esempio quella del display) nell'inizializzazione della SD. fix(template methods) : spostati i metodi dal .cpp al .hpp. fix(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
2026-06-05 add(ui_vars_mutexs.c) : aggiunto il file in cui sono dichiarati i mutex che verranno esternati dal .h.
    fix(extern C) : risolto il problema della funzione ui_init_var_mutexs() che non riusciva ad essere esternata perchè il file è .c quindi bisogna fare il controllo e vedere se è definito __cplusplus
    [ui_vars_mutexs.c]
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2026-06-06 fix(undefined MILLIS for microSD log).
    chore(Queue Length) : aumentata la lunghezza della coda di log da 20 a 100 logs.
    disabled(WiFi Init, Log MQTT and Copy To SD) : disabilitati perchè attualmente rallentano un po' e "sporcano" il programma.
    bug(string "message" resize) : il resize della stringa corrompe l'HEAP, momentaneamente disattivato.
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2026-06-09 add variable to error buttom
    [vars.h]
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2026-06-12 refactor(Logger logic) : ora il debugger assembla il messaggio nella task.
    substitute(Queue with MessageBuffer) : sostituita la coda con un message buffer che viene considerato migliore per i log doc : https://www.freertos.org/Documentation/02-Kernel/04-API-references/09-Message-buffers/00-RTOS-message-buffer-API
    chore(LOGGER_MESSAGE_BUFF_LEN) : diminuita da 100 a 10 la lunghezza del buffer di messaggio (ex LOGGER_QUEUE_LEN)
    fix(bug colors in restartESP32()) : scrive direttamente il codice ANSI del bold red.
    add(LOG_ACTIVE_SERIAL) : ora si può decidere se attivare i log nella seriale.
    refactor(Serial Init) : ora la seriale viene inizializzata anche se i log non sono attivi.
    refactor(MQ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
2026-06-12 fix(begin()) : risolto un problema legato all'assegnazione del flag "changeOccurred" e del level che sovrascriveva il valore reale portando ad errori
    add(MUTEX_TICKS) : aggiunta la possibilità di far aspettare qualche millisecondo per prendere il semaforo, per ora definito a 100ms massimo
    fix(comments) : aggiustati dei commenti nella definizione della classe e portato tutte le variabili da private a protected
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2026-06-15 fix jogger page call
    [screens.c, vars.h]
2026-06-15 exp fix WiFi 2
    [screens.c]
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2026-06-15 exp fix hmi 2
    [screens.c]
2026-06-15 exp fix Wifi 3
    [screens.c]
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2026-06-17 fix(easter egg page) : risolto il problema della variabile non nativa che veniva chiamata al di fuori di eez-flow.
    [screens.c, vars.cpp]
2026-06-17 add(Time & Date) : aggiunta la visualizzazione della data e dell'ora nella UI. L'RTC viene sincronizzato con il server NTP "pool.ntp.org" ogni 30 minuti per evitare drift accumolati e non dover avere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
    [tasks_cfg.hpp]
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2026-06-18 fix(duplicated random rows) : rimediato ad un errore di merge in cui si era fatta una duplicazione di diverse righe del codice principale.
    [DecapsulatorPRG.cpp]
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2026-06-18 add(lvgl logs) : è possibile ora attivare i logs della libreria lvgl.
    fix(touch calib datas from SD) : venivano impostati i dati di calibrazionie del touch base e non quelli salvati in SD ma anche fosse stato corretti se c'era un problemadi corruzione con i dati di calibrazione del touch memorizzati in SD sarebbero stati inseriti dati sbagliati.
    update(UI refresh from 30Hz to 60Hz).
    remove(comments and old debug logging).
    [HMI.cpp]
2026-06-18 upgrade(lvgl config) : ora la configurazione della libreria lvgl costa meno in termini di risorse al sistema. In più è stata aumentata la frequenza di aggiornamento del display.
    fix(out of memory issue WiFi Config) : risolto il problema che la UI andava out of memory quando si entrava nelle configurazioni del WiFi
2026-06-19 fix(setDuty) : caricava in ledcWrite this-> duty (che non è mai settato) al posto di duty_percentage (che è il nuovo duty dell'utente.
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2026-06-21 refactor(remove accelerations) : rimosse le accelerazioni per problemi quando il driver non riusciva ad essere aggiornato con update() nelle fasi di acc e dec e quindi perdeva passi risultando in una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
2026-06-21 fix(Jogger Handling) : gestione corretta dei fine corsa dei motori
    [JogMotoriPRG.cpp, screens.c]
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2026-06-21 fix qr when error
    [screens.c]
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2026-06-24 add(force ESP.restart) : forza l'ESP a resettarsi in caso di cadute di tensioni poichè non è più garantita la posizione reale dei motori.
    [AutoKillPRG.cpp]
2026-06-24 fix(log path) : per errore era stato scritto "log.h" al posto di "log.txt"
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2026-06-24 refactor(DebPinHandler)
    fix(safe interrupt attach) : ora viene verificato che il pin sia valido prima di fare attach di un interrupt (prima causava crash).
    fix(safe digitalWriteFast in method rawRead()) : aggiunto il controllo della validità del pin prima di leggerlo (prima causava crash.
    add(safe class destructor) : ora il distruttore della classe controlla che il mutex non sia nullptr, prova a prendere il mutex con tempo indeterminato, se è interrupt e Attach e il pin è valido allora detach del pin di interrupt.
    add(isAttached() method) : aggiunto il metodo per verificare che un pin sia attached.
    add(generic update() method) : aggiunto un metodo per fare l'update generico indipenden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
2026-06-24 fix(_tmrStartOfRmtTransmit) : _tmrStartOfRmtTransmit era in millisecondi (millis()) ma deve essere in microsecondi (micros()).
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2026-06-24 STABLE RELEASE
    remove(ptrAutokillSharedVars).
    add(skipOneLoadingPhase) : aggiunto un flag per skippare un'apertura del ServoParatia nei seguenti casi : post homing, restart, stop, errore bloccante.
    remove(auto fun off) : rimosso lo spegnimento della ventola perchè per garantire che essa non perda la posizione quindi la ventola deve raffreddare sempre.
    fix(SERVO_OPEN) : fixata l'apertura del ServoParatia
    remove(PUNCHER_SLOW _STATES) : rimossi gli stati in cui il punzone va piano.
    add(Autokill Notify) : aggiunta la notifica dell'Autokill che invia in coda i dati del programma principale.
    [DecapsulatorPRG.cpp]
2026-06-24 WIP fix(pods count) : fix da testare di tracking delle capsule nelle varie fasi.
    fix(CONTAINER_FULL_STATE get_var_pulsante_errore busy wait) : aggiunto un delay per lo yield.
    remove(legacy accelerations): rimosse completamente le accelerazioni.
    [DecapsulatorPRG.cpp]
2026-06-24 refactor(homing) : messo l'homing corretto (non testato) del decapsulator.
    add(xQueue resets) : le queues dei Jog- e Jog+ vengono resettate quando si disabilita il motore per evitare avviamenti accidentali.
    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
    [JogMotoriPRG.cpp]
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2026-06-25 replace(nCicliRimanenti): sostituita nCicliRimanenti con shiftRegisterCapsuleCaricate
    [AutoKillPRG.cpp]
2026-06-25 fix(reset __isHomeFinished __isHomeFailed when calling home()) : aggiunto il reset dei flag che prima non permettevano all'homing di essere rieseguito.
2026-06-26 fix(crash screen "Avvio Macchina") : aggiunto il lock quando aggiorna l'lvgl timer e alla variabile nelle funzioni condivise così non crasha più quando si prova a passare dallo schermo di avvio macch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
    [HMI.cpp, vars.cpp]
2026-06-26 fix(contatori capsule) : aggiunto uno shift register per contare le capsule e sapere esattamente dove sono nel tamburo.
    add(gestione fault motori) : ora i motori fanno aspettare l'utente un po' fino a quando i driver dei motori non si sono raffreddati.
    fix(post Homing position Ralla) : impostato correttamente la posizione post Homing della ralla.
    add(motors attach only when needed) : ora i motori vengoni messi in coppia (abilitati) solo quando serve utilizzarli, il tamburo in realtà rimane sempre in coppia per poter garantire la posizione, se perde la coppia viene rifatto l'homing (se viene rilevata dal fault).
    [DecapsulatorPRG.cpp]
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2026-06-26 replace(WiFi change credentials) : aggiunta la notifica e il tentativo di connessione del WiFi con le nuove credenziali al posto di bloccare la task di HMI ora l'action_verify_wi_fi notifica la task 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
    [actions.cpp]
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2026-06-30 fix(warning 7 enumeration values not handled in switch: 'EMERGENCY_STATE', 'CONTAINER_FULL', 'TIMEOUT_STATE' from clangd compiler) : aggiunto il default case nello switch.
    [DecapsulatorPRG.cpp]
